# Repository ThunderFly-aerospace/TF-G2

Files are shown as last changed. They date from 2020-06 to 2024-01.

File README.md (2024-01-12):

# TF-G2 - Unmanned Autogyro Development Kit




Click on the following video to quickly get an overview: 
ThuderFly_TFG2_training_autogyro_prototype (http://www.youtube.com/watch?v=6PtS-MwnM_8)

[TF-G2](https://www.thunderfly.cz/tf-g2.html) autogyro is well-suited for training UAV operators and for gaining experience with autogyro mission planning. TF-G2 is limited to light payloads, but it shares all the specific properties of larger autogyros in our offering. It may find application in less demanding flight operations, however, its main purpose is to be a tool for low-cost application practice. The autogyro’s small size leads to easy transport, repairs, and maintenance.
To enhance the ease of learning autogyro technology, we made it possible to [simulate TF-G2 flight](https://github.com/ThunderFly-aerospace/PX4-FlightGear-Bridge) prior to the real flight training.

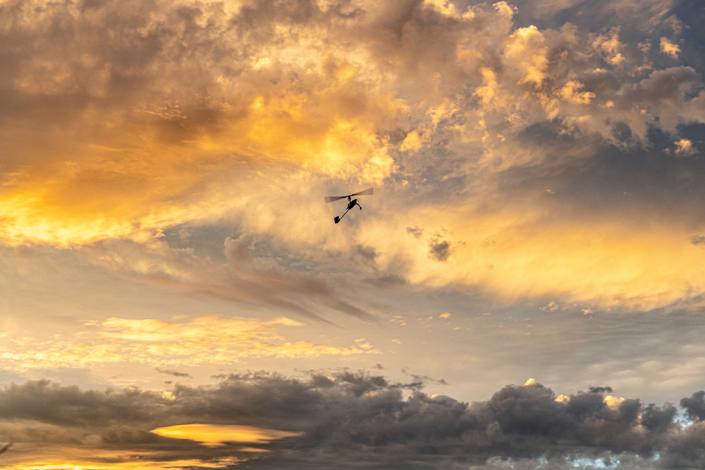
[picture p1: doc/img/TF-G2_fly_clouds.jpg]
TF-G2 during flight


## The main design highlights

  * Micro payload load capacity suitable for multiple types of [TF-ATMON atmospheric sensors](https://www.thunderfly.cz/tf-atmon.html)
  * Low audible noise
  * High maneuverability and agility
  * Extreme tolerance to rotor blade damage
  * Repairabile and low maintenance
  * Use of 3D printing flexibility
  * [Simulation model available](https://github.com/ThunderFly-aerospace/FlightGear-TF-G2)
  * [Car roof takeoff ready](https://github.com/ThunderFly-aerospace/TF-SIMPLEPLATFORM)

Based on that features the TF-G2 is perfectly suitable for [atmospheric measurement applications](https://www.thunderfly.cz/tf-atmon.html). That could be illustrated by the [successful integration of multiple sensor types](https://github.com/ThunderFly-aerospace/TFUNIPAYLOAD01). 

## Applications
Here are some examples of existing use cases for TF-G2 as a lightweight sensor carrier. These application-specific use cases extend the integrated sensing possibilities provided by existing autogyro avionics. The inherently existing onboard sensors in avionics are position, time, wind speed direction and velocity, and atmospheric pressure.

### Particulate matter sensing

Particulate matter sensing in the atmosphere is a scientific technique used to monitor and measure the concentration of small solid particles suspended in air, often termed as aerosols. These particles, typically categorized by their size - such as PM2.5 and PM10 - can originate from various sources including combustion processes, industrial emissions, vehicle exhausts, and natural phenomena like dust storms. Sensing and monitoring particulate matter is crucial for environmental health and public safety, as high levels can severely impact air quality, contributing to respiratory and cardiovascular diseases. Moreover, this data aids meteorological predictions and climate models, as particulates influence atmospheric visibility, and can affect the earth's radiation balance, hence playing a role in climate change. The TF-G2 autogyro could be equipped by [TFPM01](https://github.com/ThunderFly-aerospace/TFPM01) particulate matter sensor to measure the concentration of particulate matter in the specified air volume. 

Watch the video (https://www.youtube.com/watch?v=KUhktPDEi8I)

### Humidity and temperature sensing

Humidity and temperature sensing in [atmospheric vertical sounding](https://en.wikipedia.org/wiki/Atmospheric_sounding) involve the measurement of atmospheric moisture content and temperature at various altitudes. Instruments like the [TFHT01 sensor](https://github.com/ThunderFly-aerospace/TFHT01)  from ThunderFly are pivotal in collecting this data. These compact and lightweight sensors, designed specifically for UAV applications, can withstand varied atmospheric conditions and provide accurate, high-resolution measurements. Acquiring this data is essential for meteorological forecasts and climate studies, as the vertical distribution of temperature and humidity influences weather patterns, storm development, and overall climate dynamics. The [TFHT01](https://github.com/ThunderFly-aerospace/TFHT01) sensor, with its specialized design and precise data, has become an instrumental tool in advancing our understanding of these complex atmospheric processes.

TF-G2 atmospheric sounding experiment

An example of an atmospheric profiling experiment. The time difference between the reference and the experiment was around 6 hours. 

### Electric field monitoring

Electric field monitoring via TF-G2 UAV autogyro near thunderstorms entails the measurement of atmospheric electrical properties associated with storm activities. The charged particles present in thunderstorms create strong electric fields, which can be accurately detected and monitored by [THUNDERMILL01 sensor](https://github.com/UniversalScientificTechnologies/THUNDERMILL01). The TF-G2 autogyro, equipped with specialized sensors, can navigate challenging weather conditions and provide critical, real-time data on the strength and spatial distribution of the electric fields. Understanding these fields is crucial in predicting lightning activity, improving weather forecasts, and contributing to research on storm dynamics and atmospheric electricity. This UAV-autogyro technology offers a unique, mobile platform to safely investigate these intense electrical phenomena without putting human lives at risk.

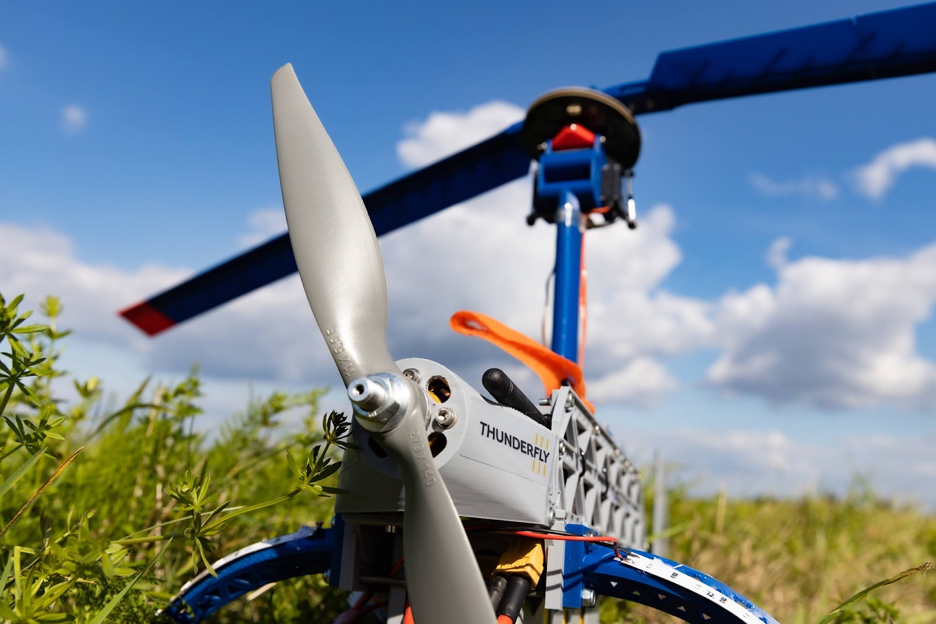
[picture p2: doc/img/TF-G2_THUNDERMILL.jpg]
TF-G2 with installed THUNDERMILL electric field sensor


### Ionising radiation monitoring

Ionizing radiation monitoring in the atmosphere involves detecting and quantifying radioactive particles using specialized devices like semiconductor-based ionizing radiation [AIRDOS03](https://www.ust.cz/UST-dosimeters/AIRDOS/#airdos03-uavdos) spectrometer and dosimeter. This instrument measures the intensity and spectral distribution of ionizing radiation, such as alpha, beta, gamma, and X-ray emissions that can originate from natural sources or human activities. The compact and precise nature of semiconductor-based devices allows for sensitive detection and accurate quantification of radiation levels. Monitoring atmospheric ionizing radiation is vital for assessing environmental radiation hazards, managing nuclear emergencies, and supporting research in fields such as meteorology, geology, and climate science. These advanced devices help ensure public safety and enhance our understanding of natural and anthropogenic radioactive processes in the atmosphere.

## Why autogyro? 

Autogyro

In contrast to the well-known [VTOL](https://en.wikipedia.org/wiki/VTOL) aircraft designs. The autogyro could be considered a short take-off and vertical landing aircraft ([STOVL](https://en.wikipedia.org/wiki/STOVL)). Therefore it is suitable for a wide range of different applications. The main advantages to other well-known airframes: 

* Ability to take off and land using only a very short runway (almost zero length).
* High resistance to weather conditions, especially gusts of wind or thermals.
* A unpowered rotor enabling it to operate in an autorotation mode (one of the helicopter’s emergency modes as well). Consequently, it does not need to actively change a flight mode in case of failure (it does not need a parachute or other actively working devices). Its flight is thus inherently stable and safe at all times.
* Autogyro has significantly reduced audible noise due to the slowly rotating rotor and propeller. 
* Absence of a downwash - during take-off or landing the creation of an unwanted swirling of dust is eliminated.
* Low lift-to-drag ratio that can be adjusted by construction parameters. This ability can be useful because an unmanned autogyro cannot fly very far in the case of controls failure (as is the case of a conventional airplane), the flight is still safe and the autogyro cannot fall (as is typical for multi-copters or wrongly piloted helicopters).

The autogyro has generally many construction variants. The one, which is in the scope of this repository has a fully tilted rotor. The main advantage of this construction feature is obtaining better controllability over its wide airspeed range. It can also be controlled down to zero forward airspeeds, compared to a classical rudder/elevator setup.

## Repository content

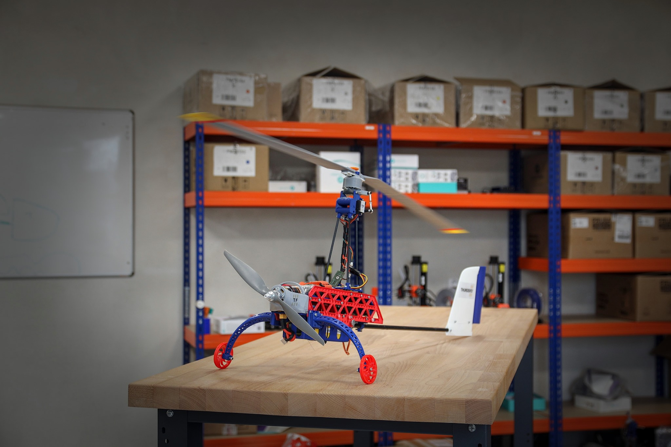
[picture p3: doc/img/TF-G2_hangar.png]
TF-G2 in hangar


This repository contains open-source design files of the autogyro construction. Most components are 3D-printed. However, the printable data (gcodes) are generated by our special software suite - processor3D. It is required that parts are sliced properly according to the material to make sure that resulted in 3D-printed parts could be used safely for the flight. **Therefore for safety reasons we do not recommend attempting to slice the parts yourself. It is better to contact us.**

The product, support, or accessories could be obtained from [ThunderFly s.r.o.](https://www.thunderfly.cz/), via an email to info@thunderfly.cz .

### Contribution

In case you want to contribute to the open-source project we have a [contribution guideline](https://github.com/ThunderFly-aerospace/TF-G2/blob/4s/CONTRIBUTING.md). Your contribution is very welcome! For a contribution, you can get access to the optimized and safe printable files (gcodes).

## References 

* [TF-G2: PX4 powered autogyro](https://static.sched.com/hosted_files/px4summit2021/ca/TF-G2%20PX4%20powered%20autogyro.pdf)
* ["Flight control system for a small autogyro" bachelor thesis](https://dspace.cvut.cz/handle/10467/101004)

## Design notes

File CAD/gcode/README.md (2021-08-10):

# TF-G2 autogyro printable gcodes

The printable data (gcodes) are generated automatically by our special software suite. It is required to ensure safety of printed parts. **Therefore for safety reasons we do not recommend to attempt to slice the parts yourself.**

The support for the product could be obtained from [ThunderFly s.r.o.](https://www.thunderfly.cz/), via an email to info@thunderfly.cz .

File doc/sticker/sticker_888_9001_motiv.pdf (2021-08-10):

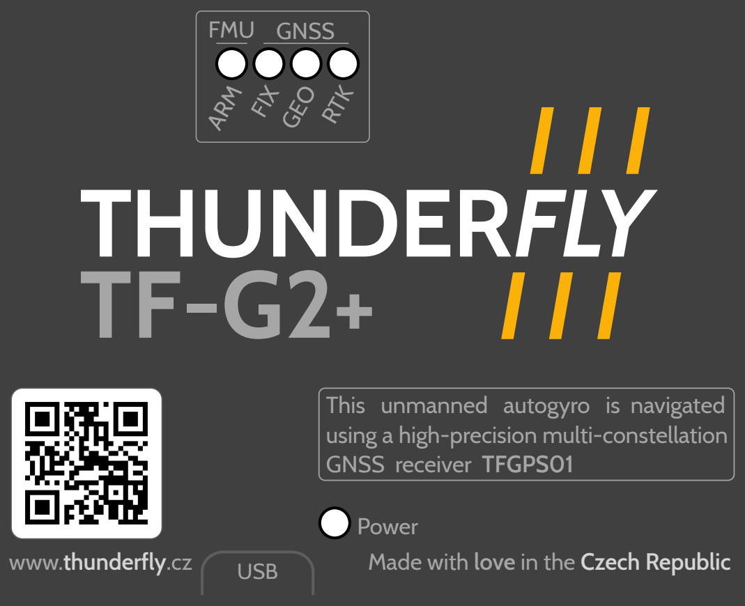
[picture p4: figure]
USB; Power; This unmanned autogyro is navigated using a high-precision multi-constellation GNSS receiver TFGPS01; ARM FIX; GEO RTK; FMU GNSS

www.thunderfly.cz | Made with love in the Czech Republic

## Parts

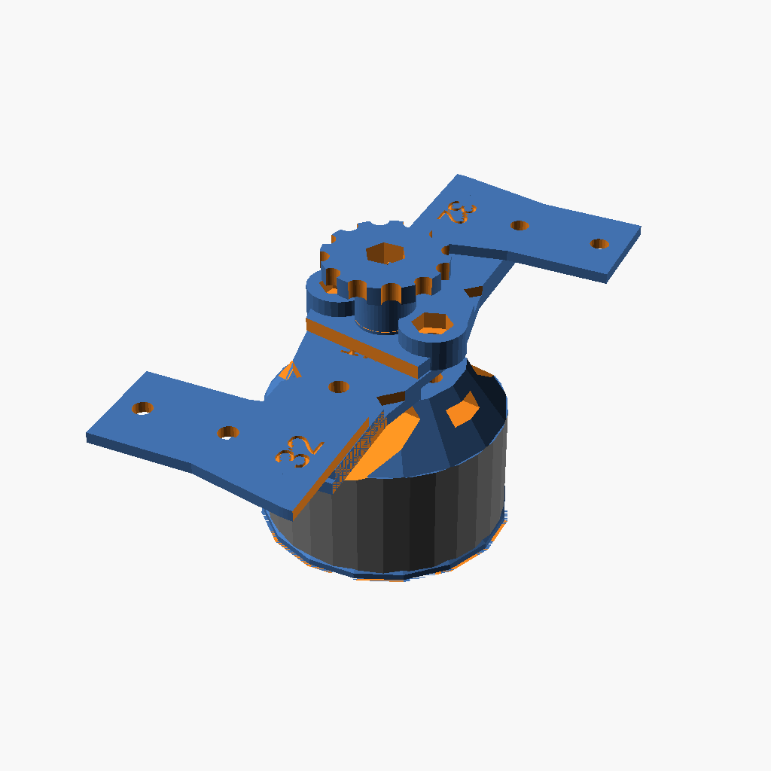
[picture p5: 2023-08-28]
CAD/png/position_rotor_parts.png

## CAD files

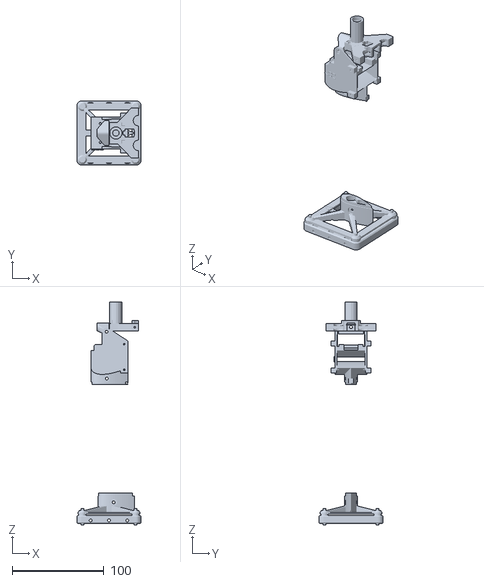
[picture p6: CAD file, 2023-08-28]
CAD/stl/assembly_pylon.stl
70.0 x 70.0 x 243.1

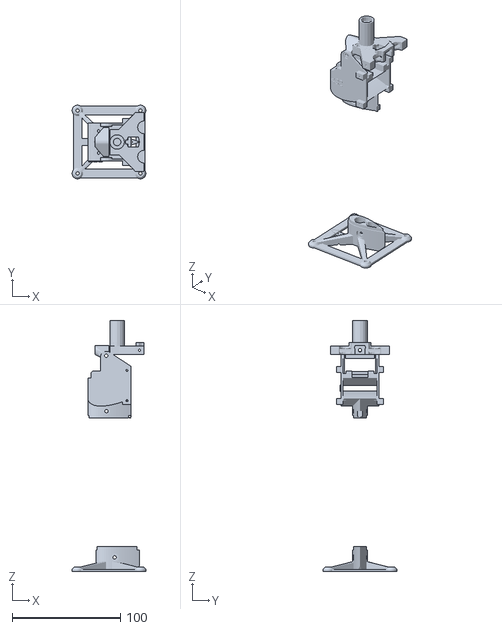
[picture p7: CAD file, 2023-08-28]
CAD/stl/assembly_rotor_head.stl
68.0 x 67.9 x 231.4

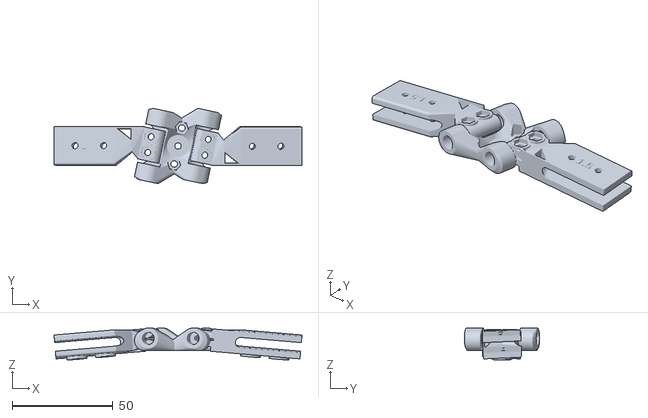
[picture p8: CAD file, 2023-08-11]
CAD/stl/assembly_freeflap.stl
122.8 x 37.3 x 15.8

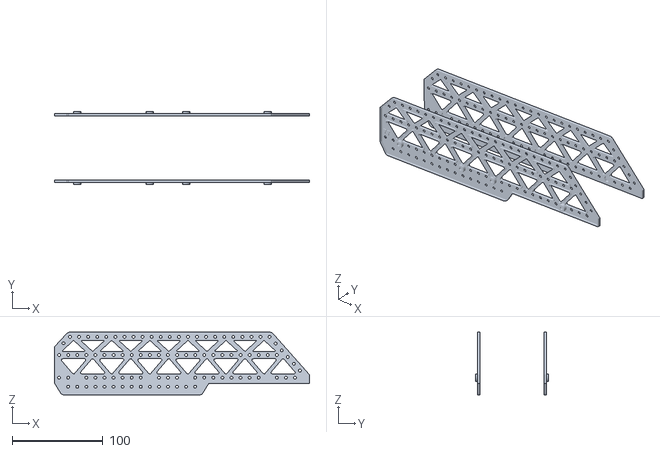
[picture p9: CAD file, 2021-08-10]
CAD/src/build_manual/stl/buildmanual_0001_c.stl
281.1 x 80.0 x 69.2

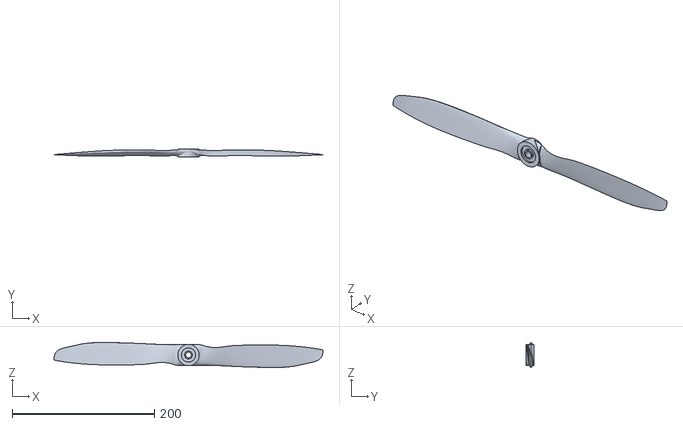
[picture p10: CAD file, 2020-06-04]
CAD/src/external_parts/APC_15x4C.stl
378.9 x 11.0 x 35.3

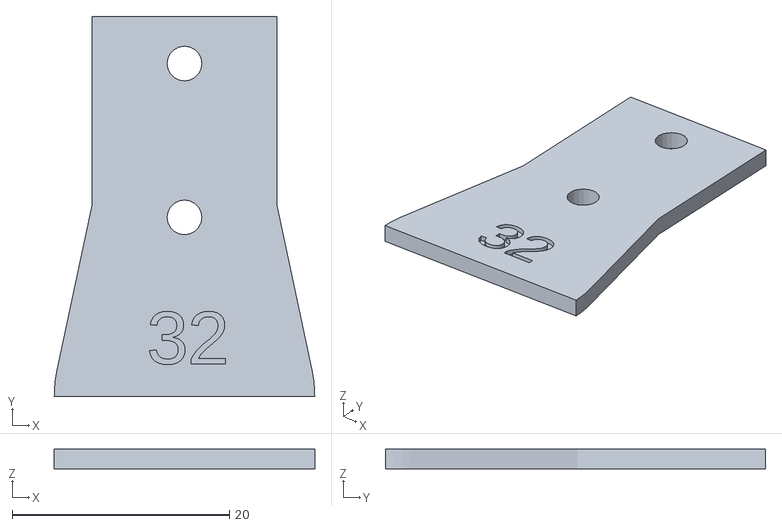
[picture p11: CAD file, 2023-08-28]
CAD/stl/888_4006.stl
24.0 x 35.0 x 1.80

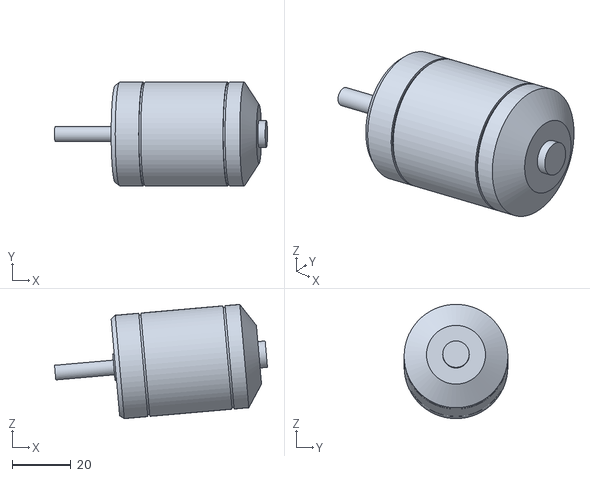
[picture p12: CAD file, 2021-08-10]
CAD/src/build_manual/stl/buildmanual_motor.stl
72.2 x 35.2 x 38.8

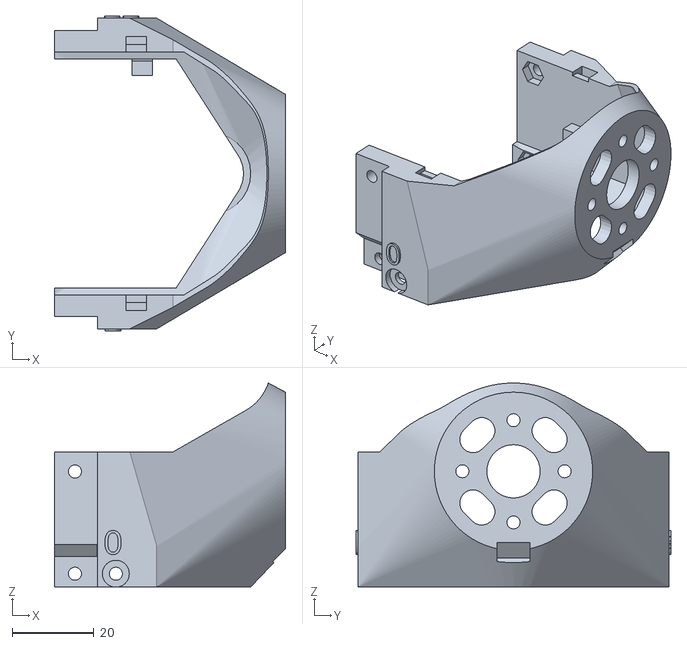
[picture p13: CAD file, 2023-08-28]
CAD/stl/888_1002.stl
56.5 x 77.0 x 49.9

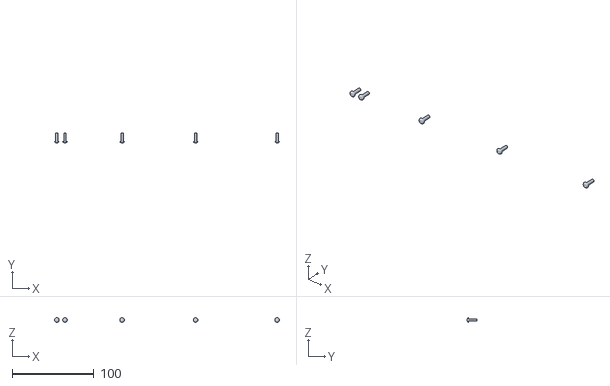
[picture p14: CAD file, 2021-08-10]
CAD/src/build_manual/stl/buildmanual_0001_d.stl
275.7 x 11.7 x 5.70

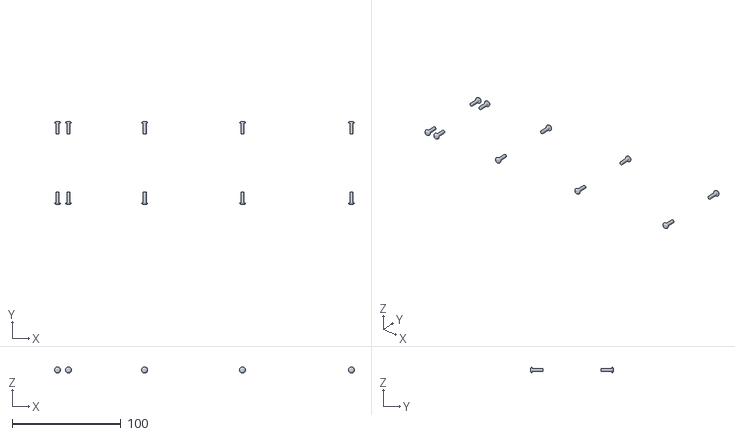
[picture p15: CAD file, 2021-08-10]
CAD/src/build_manual/stl/buildmanual_srouby_bocnice.stl
275.7 x 76.5 x 5.70

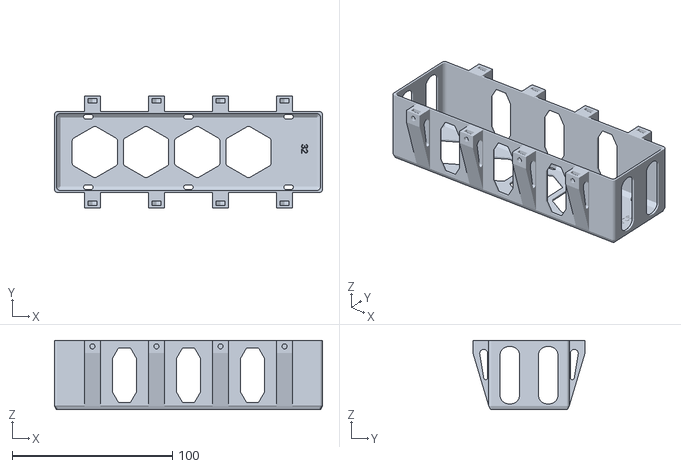
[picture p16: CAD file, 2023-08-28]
CAD/stl/position_888_1018.stl
167.4 x 70.0 x 43.2

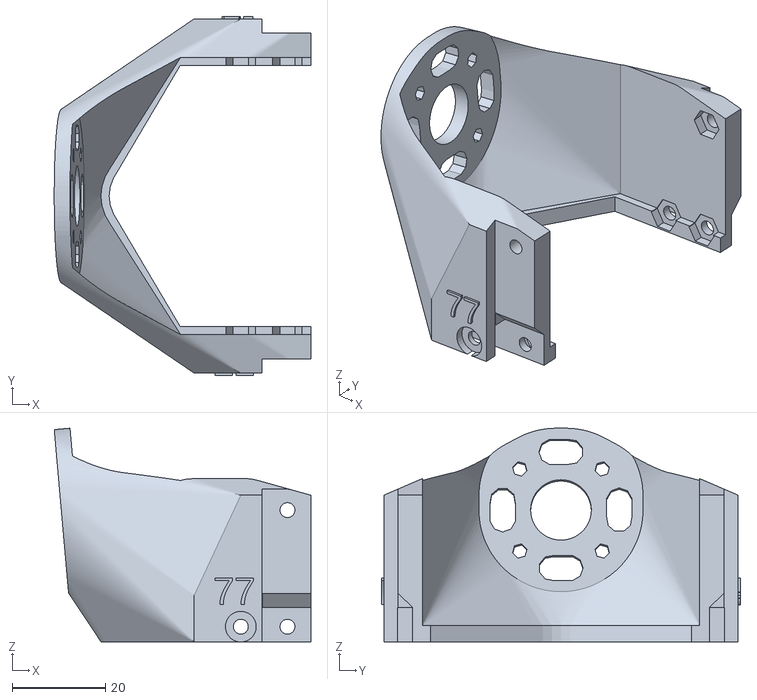
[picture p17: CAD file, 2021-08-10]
CAD/src/build_manual/stl/buildmanual_0001_b.stl
55.0 x 77.0 x 45.8

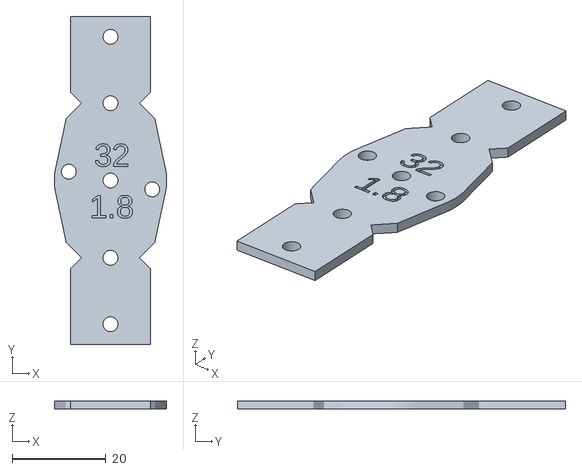
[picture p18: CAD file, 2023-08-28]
CAD/stl/888_4002.stl
24.0 x 70.0 x 1.80

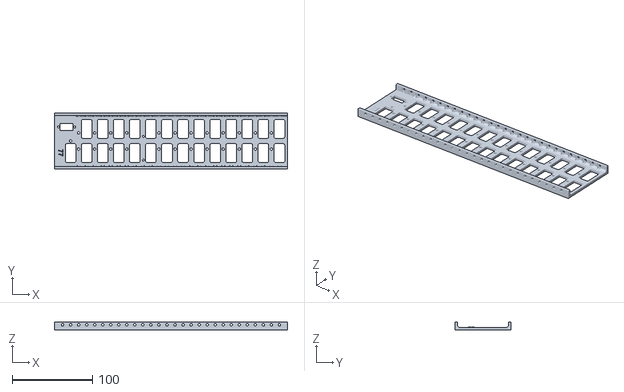
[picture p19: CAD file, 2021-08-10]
CAD/src/build_manual/stl/buildmanual_0001_a.stl
290.0 x 70.0 x 9.50

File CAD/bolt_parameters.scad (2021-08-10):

/// deprecated parameters - should be removed after code upgrade to latest libraries
///

// screw length step - minimum difference in length between two types of screws
basic_screw_length = 5;

//Screw diameter and nut for M6 [mm]
M6_screw_diameter=6.5;
M6_head_diameter = 10+0.5;
M6_head_height = 6;
M6_nut_height = 4.9;
M6_nut_diameter = 11.8;
M6_nut_pocket = 10.4;

//Screw diameter and nut for M5 [mm]
M5_screw_diameter=5.5;
M5_head_height = 5;
M5_head_diameter = 13+0.5;
M5_nut_height = 4.5;
M5_nut_diameter = 9.4;
M5_nut_pocket = 8.4;

//Screw diameter and nut for M4 [mm]
M4_screw_diameter=4.5;
M4_screw_head_height = 4;
M4_nut_height = 3.2;
M4_nut_diameter = 8.4;
M4_nut_pocket = 7.5;

//Screw diameter and nut for M3 [mm]
M3_screw_diameter = 3.2;
M3_nut_height = 2.7;
M3_nut_diameter = 6.6;
M3_screw_head_height = 3;
M3_nut_pocket = 5.6;
M3_head_diameter = 6.6;
M3_head_diameter_ISO7380 = 7.6; //https://eshop.killich.cz/signys_data/eobchod/navody/katalog/strany/iso7380a.pdf
M3_head_height = 3.0;


//Screw diameter and nut for M2,5 [mm]
M2_5_screw_diameter = 2.7;
M2_5_nut_height = 2.3;
M2_5_nut_diameter = 6;
M2_5_nut_pocket = 5.1;

//Screw diameter and nut for M2 [mm]
M2_screw_diameter = 2.0;
M2_nut_height = 1.8;
M2_nut_diameter = 4.8;
M2_nut_pocket = 3.95;
M2_head_diameter = 4.5;
M2_head_height = 2.0;

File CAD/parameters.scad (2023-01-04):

include <bolt_parameters.scad>
use <./src/lib/stdlib/naca4.scad>

week = "77";  // dummy value for visual rendering not used for printing.

global_clearance = 0.2;
clearance = global_clearance;

layer_thickness = 0.2;
base_patern = 10;

gliding_angle = 14;         // tenhle úhel by se zřejmě v budoucnu měl počítat z požadované klouzavosti.



////Simoniny parametry pro nosník rotoru
base_length = 290; //delka podlozky
base_split_position = [0, 149, base_length];
base_width = 70; //sirka podlozky - vnější šířka nosníku
base_thickness = 3; //vyska podlozky
autopilot_base_thickness = 4; // vyska podlozky vysuzujici prostor pod autopilotem
rantl_thickness = 3; //sirka steny podlozky
rantl_height = 6.5;
niy=4; //pocet der podelne

side_base_thickness = 0.2*6; // minimalni tlouska  u bocnic napr. sten



// Rotor parameters

rotor_blade_AOA = 1.5;      // nastavení úhlu náběhu rotorového listu
rotor_blade_rod = true;  // generovat diru pro uhlikove tycky
rotor_blade_length = 500;   // délka rotorového listu
// rotor_blade_length = 450 - 15;   // délka rotorového listu -- nastaveni prvniho vytisku
//rotor_blade_length = 460;   // délka rotorového listu
rotor_blade_depth = 45.5+2;     // hloubka rotorového listu
rotor_balde_tip_cutoff = 15.5;

blade_mount_length = 30;

blade_mount_width = 17;
blade_mount_thickness = 4.6;
blade_mount_screw_offset = 5; // distance of first screw from rotor end

// Testovaci maly rotor
    /*
    rotor_blade_rod = false;
    rotor_blade_length = 145;   // délka rotorového listu
    rotor_blade_depth = 45.5 * (145/385);     // hloubka rotorového listu
    blade_mount_length = 20;
    blade_mount_width = 10;
    blade_mount_thickness = 4;
    */
// konec parametru pro testovaci maly rotor

rotor_height = 180;         // výška otočného kloubu rotoru nad hlavní trubkou vírníku (odhad)
rotor_blades_count = 2;
rotor_delta_angle = 12;
rotor_blade_thickness = 5.1;
//rotor_balde_tip_cutoff = 10;

rotor_blade_naca = 2412;
rotor_blade_parts_count = 4;
//rotor_blade_parts_count = 3;

blade_transition_length = 10; // length of blade transition

blade_mount_screw_distance = (16.47+11.86)/2;

rod_from_end = 10;

/* blade_shell_thickness = 0.4;
blade_shell_thickness_inner = 0.4;
blade_shell_thickness_wire = 0.4;
blade_infill_distance = 25;
blade_infill_overlap = 0; */

/// Nastaveni pro Slic3r
blade_shell_thickness = 0.5;
blade_shell_thickness_inner = 0.08;
blade_shell_thickness_wire = 0.5;
blade_infill_distance = 23;
blade_infill_overlap = 0;

//blade_rod_position = [rotor_blade_depth/4 + 5, 0, 0];
//blade_rod_position2 = [rotor_blade_depth/4 - 5, 0, 0];

//blade_rod_position = [15, 0, 0];
//blade_rod_position2 = [4, 0.3, 0];

//blade_rod1_diameter = 2.58;
//blade_rod2_diameter = 2.58;
//blade_rod3_diameter = 2.13;
blade_rod1_diameter = 2.45;
blade_rod2_diameter = 2.45;
blade_rod3_diameter = 2.45;


// blade_rod1_position = [3.4, 0.3, 0];

blade_rod1_xposition = rotor_blade_depth/4 - 8.9;
blade_rod1_yposition = rotor_blade_depth * camberY(naca = rotor_blade_naca, x = blade_rod1_xposition / rotor_blade_depth); // calculate airfoil chamber line y position

blade_rod1_position = [blade_rod1_xposition, blade_rod1_yposition, 0];  // shift rod1 to chamber line location
blade_rod2_position = [rotor_blade_depth/4 - 5.8, 0.5, 0];
blade_rod3_position = [rotor_blade_depth/4 + 3.5, 0.5, 0];

blade_glue_holes = 0;

blade_mount_screw = M3_screw_diameter;
blade_mount_nut = M3_nut_diameter;

rotor_blade_endtip_diameter = 20;

rotor_blade_part_list = [0, 50, 200, 350, 500];


// vzdalenosti der pro kryty
//platform_mount_points = [base_patern*5, base_patern*13, base_patern*17, base_patern*26];
// Otvory pro pripevneni na platformu
platform_mount_points = [base_patern*8, base_patern*26];

cover_rantl_thickness = 0.8; // tloustka rantlu, ktery ma mit ramecek pro pripevneni a zpevneni oblecku.. 

leg_screw_dy = 20; // Vzdalenost sroubu, na ktery se upevnuji podvozkove nohy

/////
// Parametry rotorové hlavy
/////


// Parametry pro loziska rotoru

bearing_outer_diameter = 10.2;
bearing_thickness = 4;
bearing_shaft_length = 20.6;


////
//
//	Navrh geometrie rotorove hlavy vychazi z nakresu od Dobiase
//
////

rotor_head_plate_thickness = 5;
rotor_ball_joint_neck = 3; // vyska krcku tahla od stredu koule.


// parametry pro dil, co se naklapi v roll a pitch, obsahuje tfprobe

// delka dilu v podelne ose virniku - od osy pitch
rotor_head_rod_x = 35;
// sirka dilu na stredy tahel
rotor_head_rod_y = rotor_head_rod_x*2 - rotor_ball_joint_neck*2;
// vyska dilu az po rovinu rotoru
rotor_head_rod_z = 0;

rotor_head_shaft_angle = 10;



rotor_head_pitch = 0;
rotor_head_roll = 0;



// Engine and engine holder parameters

motor_holder_height = base_patern * 5;
motor_holder_thickness = 3.5;
motor_holder_motor_height = 25;
motor_holder_side_mount_height = base_patern*2.5;
pylon_holder_side_mount_height = base_patern*4.5;

engine_angle = 0; // ongle of engine axis relative to fuselage main axis
engine_diameter = 55;
engine_offset = 53;			// Posun motoru v ose X (dopredu)




// Parametry pro hacek na kabely od motoru
	motor_wire_holder_width = 5;
	motor_wire_holder_height = 10;
	motor_wire_holder_space = 3;
	motor_wire_holder_thickness = 2.5;
	motor_wire_holder_z_shift = 10;
	motor_wire_holder_x_shift = 19;

// Parametry pro ochranny ram nad motorem
	motor_protective_frame_x_shift = 20;
	motor_protective_frame_z_base = 32;
	motor_protective_frame_beam_width = 5;
	motor_protective_frame_beam_thickness = 3;
	motor_protective_frame_width = base_width-3;
	motor_protective_frame_plug_thickness = 2;
	motor_protective_frame_plug_length = 4;
	motor_protective_frame_thickness = 5;
	motor_protective_frame_z_scale = 0.75;


//sroub servo
Servo_screw = 1.5;
Servo_nut_height = 1;
Servo_nut_diameter = 2.7;

tail_pipe_d = 13.04;

// elevator parameters

elevator_pitch = 2; // elevator pitch relative to main fuselage axis

/// rudder parameters

rudder_height = 150;
height_bottom_part = 130;
rudder_depth_max = 200;
rudder_inclination = 25;

below_rudder_height = 30;
rudder_depth = 60;

tail_airfoil_n = 80;

//center_of_gravity_position = [main_pylon_position - tan(gliding_aggle)*rotor_height, 0, 0];


////landing gear

radius_undercarriage = 25;
vzdalenost_x = tan(20) * 131;
vzdalenost_y = (131 - radius_undercarriage)/tan(79);
uhel_y = 90 - 20;
uhel_x = 90 - 79;

maximum_printable_size = 150;

// FIXME: Jak zapnout figerglass z procesoru3d ?
// fiberglass_gear = false;


// Rotor pylon parameters


// pylon_height = 250 - pylon_holder_side_mount_height;

pylon_pipe_counterbore = 24;  // delka zapusteni pylonove tyce do dilu nahore
pylon_pipe_counterbore_bottom = 20;  // delka zapusteni pylonove tyce do dilu dole
pylon_pipe_screw_distance_from_top_end =  17;
pylon_pipe_screw_distance_from_bottom_end =  10;


pylon_pipe_top_offset = 6; // Jak hluboko do TFSLOTU lze tycku pylonu zapustit..
pylon_airfoil_shell_overlap = 3;  // presah profilu (krytu) pylonu a montaznich casti (spodnyi a horni objimka)

pylon_pipe_d = 10.3;
pylon_suspension_height = 150;
pylon_pipe_top_dist = 0;
pylon_thickness = 0; // Netusim, co to je

pylon_bottom_wall = 5;

pylon_silentblocks_base_distance = 58;    // vzdalenost silentblocku pylonu od sebe
pylon_pipe_top_y_dist = 25;
pylon_pipe_top_x_dist = 30;
pylon_screw_top_y_dist = 25;
pylon_screw_top_x_dist = 15;

pylon_height = 180 + 50 - pylon_holder_side_mount_height;

airspeed_width = 35;
airspeed_naca = 0004;
airspeed_dist = 20;


// Parametry k akumulatoru

//battery_type = "Zippy_4S_3700";
//  GensACE 3300 mAh

//free-flap-head
free_flap_ax_length=36;
free_flap_ax_diameter=3;

free_flap_bearings_length=9.8;
free_flap_bearings_outer_diameter=6.2;
free_flap_bearings_ring_diameter=9;
free_flap_bearings_ring_h=1.5;
//free_flap_bearings_outer_diameter=3;
free_flap_negativ_flap_limit=5;
free_flap_bearing_add=4;
free_flap_desk_add=1;
free_flap_desk_h=2.5;

free_flap_delta_angle=-rotor_delta_angle;
free_flap_blade_screw_distance=blade_mount_screw_distance;
free_flap_central_part_screw=3;
free_flap_central_part_screw_distance=3 + 4.5 + blade_mount_screw/2;

free_flap_circle_fn=40;

free_flap_ax_offset=6+free_flap_bearing_add/2+free_flap_bearings_outer_diameter/2;

free_flap_shaft_l=free_flap_ax_length-2*free_flap_bearings_length;
free_flap_shaft_h=free_flap_ax_diameter+free_flap_bearing_add;
free_flap_shaft_neck_l=7;

free_flap_cut_d=12;
free_flap_cut_h=10;
free_flap_cut_w=5;

free_flap_blade_d=20;
free_flap_blade_holder_h=3;

free_flap_blade_holder_l=blade_mount_length;
free_flap_blade_h=blade_mount_thickness+0.5;
free_flap_blade_w=19;
free_flap_blade_first_screw=blade_mount_screw_offset+0.5;

free_flap_blade_holder_radius=0.7*free_flap_blade_holder_h;


//if(battery_type == "GensACE_3S_3300"){
	// battery_case_height = 25;
	// battery_case_start_x = 25;
	// battery_case_wall = 1;

	// battery_width = 50;
	// battery_height = 20;
	// battery_length = 150;

	// battery_capacity = 3300;
	// battery_cells = 3;
//}
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

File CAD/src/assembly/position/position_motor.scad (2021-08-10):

include <../../../parameters.scad>
use<../../lib/stdlib/motors.scad>

translate([base_patern*3, 0, motor_holder_side_mount_height])
translate([0, 0, 4])
rotate([0, -90-5, 0]) motor_c3548_900();

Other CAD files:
CAD/amf/printplate_888_1016_front.amf
CAD/stl/888_4008.stl
CAD/stl/888_1010.stl
CAD/stl/position_rotorhead.stl
CAD/src/build_manual/src/buildmanual_motor.scad
CAD/blender/TF-G2_flow.blend
CAD/blender/colours.blend
CAD/blender/title.blend
CAD/src/888_1001.scad
CAD/src/888_1002.scad
CAD/src/888_1003.scad
CAD/src/888_1004.scad
CAD/src/888_1006.scad
CAD/src/888_1007.scad
CAD/src/888_1008.scad
CAD/src/888_1009.scad
CAD/src/888_1010.scad
CAD/src/888_1011.scad
CAD/src/888_1012.scad
CAD/src/888_1013.scad
CAD/src/888_1018.scad
CAD/src/888_1019.scad
CAD/src/888_1020.scad
CAD/src/888_1021.scad
CAD/src/888_2002.scad
CAD/src/888_2003.scad
CAD/src/888_2004.scad
CAD/src/888_2005.scad
CAD/src/888_2006.scad
CAD/src/888_2007.scad
CAD/src/888_3001.scad
CAD/src/888_3002.scad
CAD/src/888_3004.scad
CAD/src/888_3006.scad
CAD/src/888_4001.scad
CAD/src/888_4002.scad
CAD/src/888_4003.scad
CAD/src/888_4004.scad
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

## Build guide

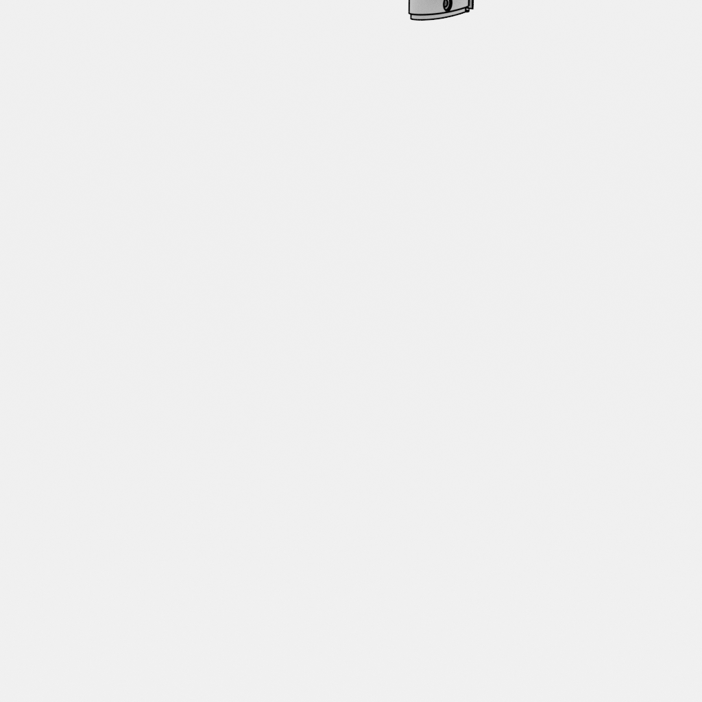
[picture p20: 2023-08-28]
doc/assembly_guide/img/TF-G2_assembly_rotorhead_complete.png

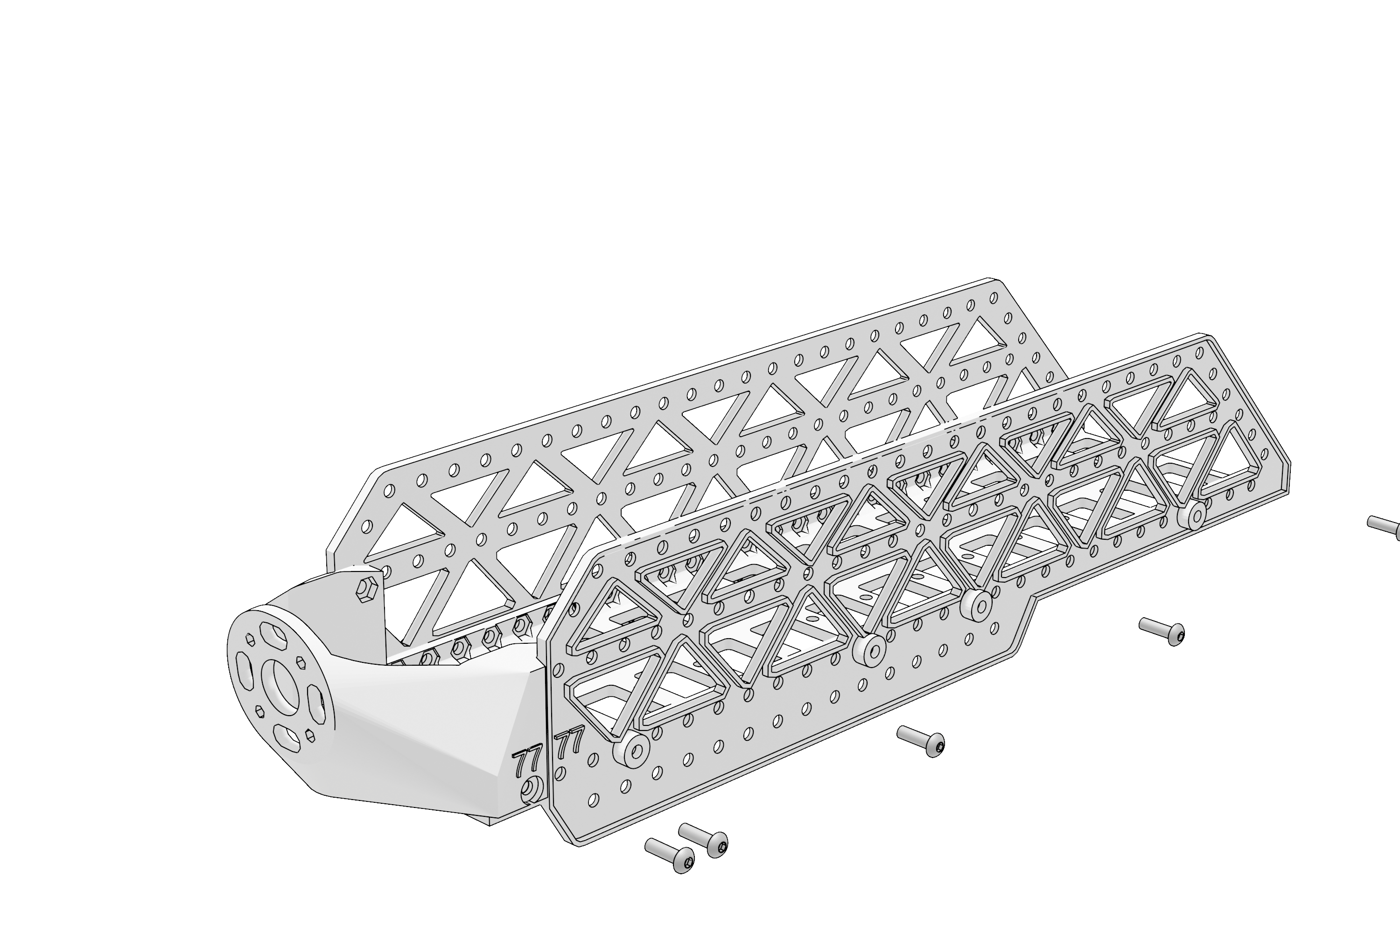
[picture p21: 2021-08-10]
doc/assembly_guide/src/buildmanual_0001.png

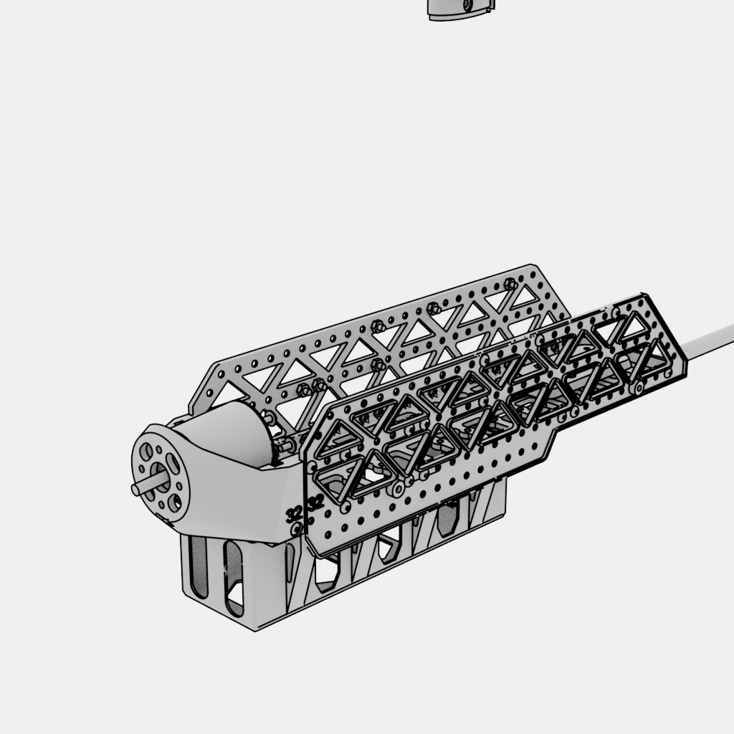
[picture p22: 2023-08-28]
doc/assembly_guide/img/TF-G2_assembly_chassi.png

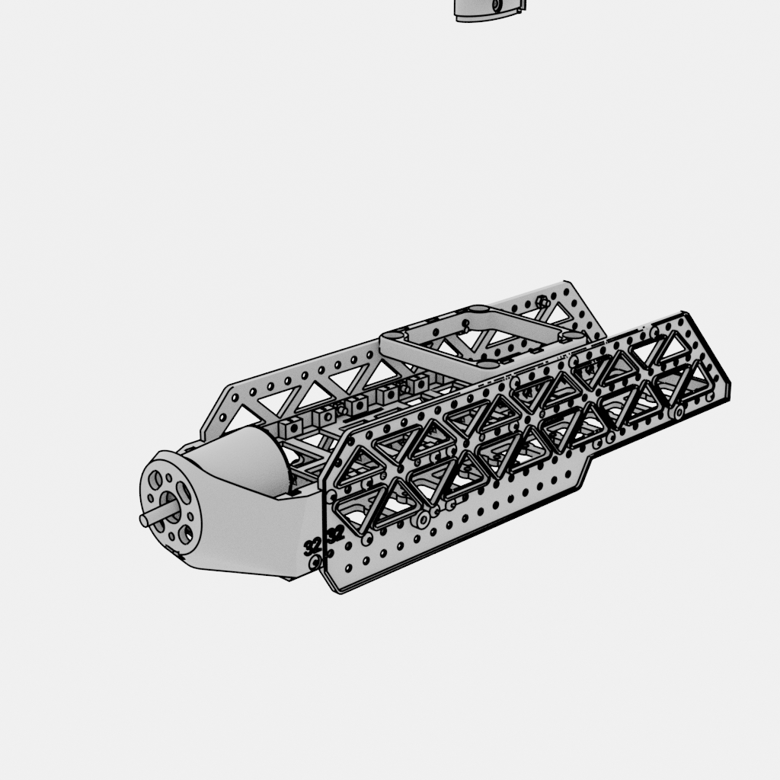
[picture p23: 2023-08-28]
doc/assembly_guide/img/TF-G2_assembly.png

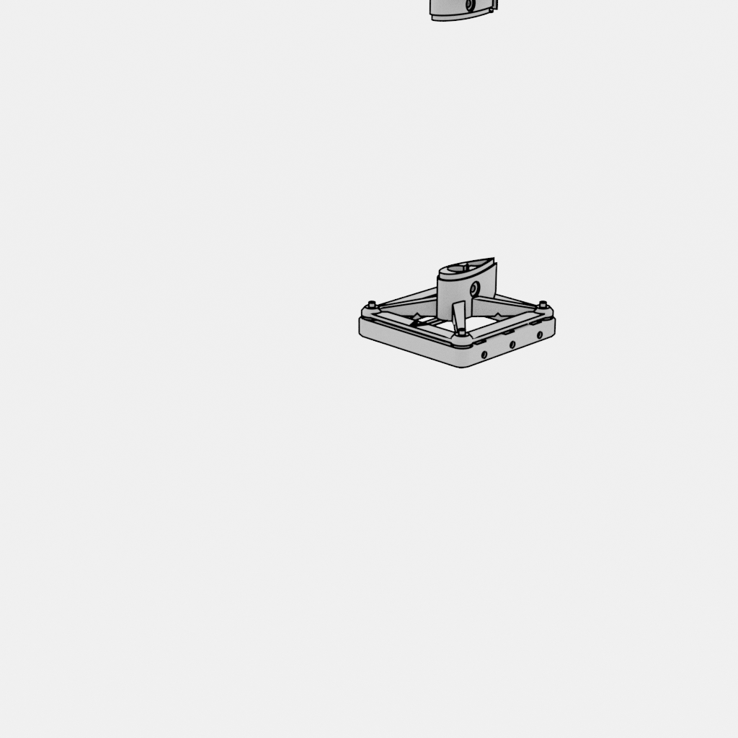
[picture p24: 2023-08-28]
doc/assembly_guide/img/TF-G2_assembly_pylon.png

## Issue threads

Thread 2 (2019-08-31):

Nosná podložka

roman-dvorak, 2019-08-31:
K dovyřešení:
- [ ] Vyřešit způsob připevnění předního podvozku.
---
 - [X] Základní návrh (done by @zelenac)
 - [X] Úprava rozměrů a prvotní vytvoření odlehčovacích otvrů (done by @roman-dvorak)
 - [x] Optimalizace hmotnosti: Chytřejší otvory pro odlehčení
 - [x] Místo na připevnění podvozku
 - [x] Zapuštění matek v postranním rantlu.
 - [X] Rozšířit podložku o 10 mm (celková šířka 70 mm), @roman-dvorak
 - [x] Chybí díra pro přišroubování držáku motoru do podložky.
---

Nosná podložka malého vírníku se bude skládat ze dvou identických částí.

Budou to 2 destičky, které se následně vzájemně sešroubují ~pomocí nějaké vytištěné spojky~.
Destička bude mít podélně vyšší límec, který bude mít dva úkoly. Zpevnění celé konstrukce. Vytvoření míst pro připevnění bočních stěn.

~Podložka bude 55 mm široká a dlouhá 2x140 mm~ (staré údaje). Tato délka byla zvolena z technologických důvodů - maximální tiskový rozměr.

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

Příčný řez dílem
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

Ve spodní části budou díry na šrouby na připevnění dalšího příslušenství. Budou zarovnané do nějaké určité mříže. Předpokládám nějakých 4-5 řad. Budou to díly na M3 šrouby.

Všechny rozměry musí být udělány pomocí proměnných parametricky.

roman-dvorak, 2020-04-02:
Nosná podložka je aktuálně ve stavu, že obsahuje boční lem s řadou děr pro připevnění bočnic. Podložka bude dělena na 2 časti. Na obrázku to je naznačeno. Bočnice budou na 3 časti a je potřeba zajistit, aby předěl částí nevycházel na stejné místo.

Od původního modelu došlo k odlehčení vytvořením vetších otvorů ve dnu modelu. Tyto otvory bude potřeba upravit v návaznosti na připevnění podvozku. Může pak být provedeno další odlehčení. Nebo ztečení či chytřejší vyztužení.

Na začátek první zprávy jsem vypsat věci k úpravě.

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

roman-dvorak, 2020-04-25:
Do podložky přidány šestihrany na zapuštění matky, upraveno odlehčení a otvory pro připevňení ocasu a předního podvozku.

kaklik, 2020-05-18:
Ten způsob připevnění předního podvozku na dva šrouby je podle mě vyhovující.

Closed 2020-05-25.

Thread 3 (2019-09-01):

Díl pro připevnění tažného motoru

roman-dvorak, 2019-09-01:
- [X] Úvodní návrh
 - [X] Změna připevňení k bočnicím
 - [x] Zvětšení otvoru pro středovou osu na d=10mm
 - [x] Odstranění zubu (nevhodný pro tisk)
---
Druhý díl musí zapadnout do dílu #2 a bude přišroubován zespodu pomocí M3 šroubů. Bude to taková jednoduchá placka s výřezem na boční lem na #2.

Vnější rozměr musí být stejný jako rozměr podložky. Výška bude cca 7 cm.

Pro připevnění k základní podložce #2 budou v dílu z vnitřní strany kapsy na matky - jak vypadá kapsa je popsáno na konci.

Uprostřed placky bude otvor pro připevnění motoru. To bude realizované pomocí trojice děr uspořádaných do rovnostranného trojúhelníku. Poloměr kružnice opsané (skrze středy) bude cca 1.5 cm. Bude ještě upřesněno. Výšku motoru by mělo být možné nastavovat pomocí parametru.

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

Kapsa na matku je drážka (obdélníková díra) ukončená šestihranem v díře pro šroub. Matka se do ni zastrčí a následně se šroub může skrze díru přítáhnout.

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

roman-dvorak, 2020-04-02:
Oproti původnímu návrhu byl díl značně zmodifikován. Princip zůstává stejný.

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

Potřebné úpravy jsou zvetšení středové díry a upravení kulatého tvaru nahoře tak, aby se tam nevytvářel zub způsobený uchem pro připevňení.

Closed 2020-04-25.

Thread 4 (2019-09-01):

Boční stěny

roman-dvorak, 2019-09-01:
- [X] Základní návrh
 - [X] Ovory pro odlehčení (hardcodované)
 - [x] Odstranit starou řadu otvorů pro připevnění držáku motoru
 - [x] zparametrizovat a optimalizovat odlehčovací otvory
---
Boční stěny budou přišroubovány k límci dílu #2 a #3. Díl bude potřeba rozdělit na 3 části, čímž se zároveň zajistí, že spoj nebude vycházet na stejné místo jako bude spojen spodní díl #2.

Boční stěny by měly vypadat nějak cca takto:
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

Budou obsahovat řadu děr pro sešroubování s podložkou. Boční stěna může mírně přesahovat pod podložku #2.

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

Celková výška stěny by měla být okolo cca 8-9 cm. Délka cca 33 cm. Tloušťka stěny může být cca 3 mm. Pokud to bude málo, tak je následně možné nahoře domodelovat nějaké rozpěrky, které se tam buď přišroubují nebo zalepí.

Stěna by na sobě mohla mít také síť děr pro přišroubování nějakého příslušenství. Nemusí být tak hustá jako v podložce.

roman-dvorak, 2020-04-02:
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

Otvory pro odlehčení jsou dosti hardkodované. To by bylo vhodné trochu zparametrizovat. Dále v přední časti jsou 2 řady otvorů pro připevnění. To je důsledek kompatibility starší (už vytištěné verze držáku motoru) a nového umístění otvoru. Staré umístění děr je možné smazat.

Closed 2020-04-25.

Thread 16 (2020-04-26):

Doplnění airspeed senzoru

kaklik, 2020-04-26:
* [x] vytvořit víčko airspeed senzoru držící PCB TFASPDIMU
* [x] Upravit stávající řešení pro nový snímač [TFASPDIMU02](https://github.com/ThunderFly-aerospace/TFASPDIMU02)
* [x] Vyřešit umístění TFRPM viz issue: #76 (PCB z horní strany tak, aby byla snadno vidět LED)
* [x] Možná prodloužit TFSLOT trubici

Na vírník je potřeba přidat [airspeed senzor](https://github.com/ThunderFly-aerospace/TFAIRSPD01).

Uchycen by měl být na horní části pylonu pod rotorovou hlavou. viz issue: https://github.com/ThunderFly-aerospace/TF-G2/issues/7

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

@roman-dvorak  Navrhuje celý snímač namontovat místo středního dílu na fotografii výše.  Snímač by tak byl modifikovaný pouze pro tuto konstrukci.
Současný díl na fotografii jen vymezuje vzdálenost mezi bočnicemi pylonu. Druhý účel je, že určuje úhel těch bočních dílů a zajišťuje aby jeho vnitřní strany byly rovnoběžné.  Díl obsahující snímač by všechny tyto funkce mohl kombinovat.

roman-dvorak, 2020-04-26:
Úplně původně zamýšlené místo bylo pod tím středním rámečkem, kde jsou již připravené montážní otvory. Ale ten je dost nízko (původně měl být umístěný výš). Tak je možné ho nějak připevnit až přimo pod rotor. Do toho horního rámečku.

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

kaklik, 2020-06-05:
Myslím že mě napadlo jak zjednodušit úpravu z issue https://github.com/ThunderFly-aerospace/TFASPD01/issues/1
Tak aby snimač bylo možné umístit úplně nejblíže rotorové hlavě. Venturiho snímač by tak nově byl takováto krabička:

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

Zaoblené profily jsou ve skutečnosti nějaké NACA profily a jsou symetrické dva proti sobě.  Předpokládám, že by se celá tahle hranatá věc tiskla najednou, takže to může být i nějaká přepážka sloužící k vyztužení.
Je myslím zatím i jedno, jestli bude orientována horizontálně, nebo vertikálně.
Plošný spoj se snímači by se opět přimáčkl do kanálků z vnější strany a držel by tam tím že se celý snímač k něčemu přišroubuje.

kaklik, 2020-06-18:
@ChroustJan  navrhuje přes PCB s elektronikou udělat zasouvací víčko. Výhoda by byla, že se pak celý snímač dá vyndat jako samostatný celek a nehrozí že někde na louce vypadnou těsnění, nebo PCB.

kaklik, 2020-09-30:
@roman-dvorak  udělal první prototyp venturiho poličky. Zatím je poměrně masivní.

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

Chyby, které při návrhu vznikly jsou způsobeny nedokonalým převzetím konstrukce z anemometru.

- [ ] Plošný spoj se neopírá o přívodní konektor, ale je výše. Díky čemuž jej nelze dobře upevnit vůči vyústění trubiček
- [ ] Vyústění trubiček neobsahuje zúžení, které je důležité pro vložení těsnícího o-kroužku.
- [ ] celá konstrukce je zřejmě zbytečně masivní.

roman-dvorak, 2020-10-01:
> Plošný spoj se neopírá o přívodní konektor, ale je výše. Díky čemuž jej nelze dobře upevnit vůči vyústění trubiček

aha.. tohle jsem nepochopil správně.. takže teď bude konektor ještě výše.

kaklik, 2020-10-01:
Dnes jsem přigumičkoval snímač k nově vytištěné zmenšené variantě.

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

Tohle se stane, když do toho fouknu:

    0395; 2020-10-01T20:57:45.129444; Dp: +0.00 [Pa]; T: 32.774 [degC]; MAG_HDG: +63.04; SPD_W_DP: +0.00 [km/h]
    0396; 2020-10-01T20:57:45.183406; Dp: +0.00 [Pa]; T: 32.966 [degC]; MAG_HDG: +62.98; SPD_W_DP: +0.00 [km/h]
    0397; 2020-10-01T20:57:45.237408; Dp: +0.00 [Pa]; T: 33.110 [degC]; MAG_HDG: +62.77; SPD_W_DP: +0.00 [km/h]
    0398; 2020-10-01T20:57:45.291341; Dp: +0.00 [Pa]; T: 33.062 [degC]; MAG_HDG: +62.71; SPD_W_DP: +0.00 [km/h]
    0399; 2020-10-01T20:57:45.345361; Dp: -24.00 [Pa]; T: 33.062 [degC]; MAG_HDG: +62.59; SPD_W_DP: +1.76 [km/h]
    0400; 2020-10-01T20:57:45.399374; Dp: -34.15 [Pa]; T: 33.110 [degC]; MAG_HDG: +62.70; SPD_W_DP: +2.10 [km/h]
    0401; 2020-10-01T20:57:45.453341; Dp: -38.95 [Pa]; T: 33.062 [degC]; MAG_HDG: +62.50; SPD_W_DP: +2.25 [km/h]
    0402; 2020-10-01T20:57:45.507374; Dp: -55.35 [Pa]; T: 33.253 [degC]; MAG_HDG: +62.02; SPD_W_DP: +2.68 [km/h]
    0403; 2020-10-01T20:57:45.561325; Dp: -64.85 [Pa]; T: 33.157 [degC]; MAG_HDG: +61.83; SPD_W_DP: +2.90 [km/h]
    0404; 2020-10-01T20:57:45.615369; Dp: -65.85 [Pa]; T: 33.062 [degC]; MAG_HDG: +61.66; SPD_W_DP: +2.92 [km/h]
    0405; 2020-10-01T20:57:45.669336; Dp: -74.90 [Pa]; T: 33.062 [degC]; MAG_HDG: +61.41; SPD_W_DP: +3.12 [km/h]
    0406; 2020-10-01T20:57:45.723355; Dp: -94.05 [Pa]; T: 33.157 [degC]; MAG_HDG: +61.27; SPD_W_DP: +3.49 [km/h]
    0407; 2020-10-01T20:57:45.777320; Dp: -67.15 [Pa]; T: 33.062 [degC]; MAG_HDG: +61.31; SPD_W_DP: +2.95 [km/h]
    0408; 2020-10-01T20:57:45.831347; Dp: -75.90 [Pa]; T: 33.253 [degC]; MAG_HDG: +60.68; SPD_W_DP: +3.14 [km/h]
    0409; 2020-10-01T20:57:45.885315; Dp: -71.70 [Pa]; T: 33.110 [degC]; MAG_HDG: +60.26; SPD_W_DP: +3.05 [km/h]
    0410; 2020-10-01T20:57:45.939326; Dp: -86.30 [Pa]; T: 33.110 [degC]; MAG_HDG: +59.96; SPD_W_DP: +3.34 [km/h]
    0411; 2020-10-01T20:57:45.993290; Dp: -82.25 [Pa]; T: 33.110 [degC]; MAG_HDG: +60.01; SPD_W_DP: +3.26 [km/h]
    0412; 2020-10-01T20:57:46.047329; Dp: -58.25 [Pa]; T: 33.110 [degC]; MAG_HDG: +60.58; SPD_W_DP: +2.75 [km/h]
    0413; 2020-10-01T20:57:46.101322; Dp: -111.90 [Pa]; T: 33.110 [degC]; MAG_HDG: +60.22; SPD_W_DP: +3.81 [km/h]
    0414; 2020-10-01T20:57:46.155342; Dp: -115.60 [Pa]; T: 33.062 [degC]; MAG_HDG: +60.43; SPD_W_DP: +3.87 [km/h]
    0415; 2020-10-01T20:57:46.209296; Dp: -123.40 [Pa]; T: 33.110 [degC]; MAG_HDG: +60.19; SPD_W_DP: +4.00 [km/h]
    0416; 2020-10-01T20:57:46.263326; Dp: -103.10 [Pa]; T: 33.349 [degC]; MAG_HDG: +60.30; SPD_W_DP: +3.66 [km/h]
    0417; 2020-10-01T20:57:46.317298; Dp: -74.25 [Pa]; T: 33.110 [degC]; MAG_HDG: +60.11; SPD_W_DP: +3.10 [km/h]
    0418; 2020-10-01T20:57:46.371327; Dp: -96.85 [Pa]; T: 33.110 [degC]; MAG_HDG: +60.13; SPD_W_DP: +3.54 [km/h]
    0419; 2020-10-01T20:57:46.425293; Dp: -72.90 [Pa]; T: 33.110 [degC]; MAG_HDG: +60.21; SPD_W_DP: +3.07 [km/h]
    0420; 2020-10-01T20:57:46.479305; Dp: -80.70 [Pa]; T: 33.110 [degC]; MAG_HDG: +60.26; SPD_W_DP: +3.23 [km/h]
    0421; 2020-10-01T20:57:46.533287; Dp: -22.30 [Pa]; T: 33.110 [degC]; MAG_HDG: +60.34; SPD_W_DP: +1.70 [km/h]
    0422; 2020-10-01T20:57:46.587304; Dp: -0.40 [Pa]; T: 33.110 [degC]; MAG_HDG: +60.25; SPD_W_DP: +0.23 [km/h]
    0423; 2020-10-01T20:57:46.641271; Dp: -0.10 [Pa]; T: 33.110 [degC]; MAG_HDG: +60.66; SPD_W_DP: +0.11 [km/h]
    0424; 2020-10-01T20:57:46.695276; Dp: +0.00 [Pa]; T: 33.110 [degC]; MAG_HDG: +61.02; SPD_W_DP: +0.00 [km/h]
    0425; 2020-10-01T20:57:46.749256; Dp: +0.00 [Pa]; T: 33.445 [degC]; MAG_HDG: +61.12; SPD_W_DP: +0.00 [km/h]
    0426; 2020-10-01T20:57:46.803318; Dp: +0.05 [Pa]; T: 33.157 [degC]; MAG_HDG: +60.91; SPD_W_DP: -0.08 [km/h]
    0427; 2020-10-01T20:57:46.857261; Dp: +0.00 [Pa]; T: 33.157 [degC]; MAG_HDG: +60.97; SPD_W_DP: +0.00 [km/h]
    0428; 2020-10-01T20:57:46.911293; Dp: +0.05 [Pa]; T: 33.349 [degC]; MAG_HDG: +61.18; SPD_W_DP: -0.08 [km/h]
    0429; 2020-10-01T20:57:46.965244; Dp: +0.00 [Pa]; T: 33.253 [degC]; MAG_HDG: +61.27; SPD_W_DP: +0.00 [km/h]

To stejné jsem zkoušel i s variantou s NACA profilem

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

Když do ní fouknu tak to dopadne takhle
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
roman-dvorak, 2020-11-02:
# Testování venturiho poličky

Venturiho poličku jsem připevnil na střechu auta. Cca 60 cm nad střechu.
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

### Měření
Měření bylo provedeno pomocí [skriptu](https://github.com/ThunderFly-aerospace/TFASPDIMU01/blob/TFASPD01A/sw/TFASPD_logger.py). GPS byla připojena do Omnie s LTE/GPS přijímačem a připojena do GPSD. Externí anténa byla přimagnetovaná na střechu auta.

Každé měření bylo provedeno na jiné cestě v normálním provozu. Proto podmínky byly dost nedefinované. Tento den však nefoukalo. Cílem bylo jet určité úseky s pomocí tempomatu (tedy konstantní rychlostí).

### Legenda ke grafům

- První graf je graf groundspeed z GPS X naměřený tlak z differencionálního senzoru.

- Druhý graf zobrazuje průběh měření. Modrý graf (levý sloupec) je GPS v km/h, Světle červený graf (pravý sloupec) je rozdíl tlaku v Pa.

## NACA0040, d=20

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

## NACA0045, d=20

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

roman-dvorak, 2020-11-09:
Docela výhodné bude venturiho poličku montovat obráceně (PCB nahoře) a víčko implementovat do nejvyššího dílu pylonu. Polička bude k pylonu připevňena z horní strany pomocí dvojice šroubů. Tak, jak je to v poličce aktuálně implementováno.

Toto vylepšení souvisí s jinou montáží serv #70

JanKott, 2020-11-10:
Můžete mi prosím nakreslit jaká je požadovaná změna?

roman-dvorak, 2020-11-10:
Moje představa je cca taková:

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

Asi ani není nutné, aby to byl přesně NACA profil. Víčko bude na anemometru připevněno z horní strany. Dvojicí šroubů po stranách v přední části anemometru. Cílem je anemometr co nejvíce vysunout dopředu.

V co nejzadnější části, (kde to materiál dovolí) by měla být příčná díra skrz a v ní dvě kapsy na matky. o něco nopřeději (cca 5-10 mm) by měl být ďolík (odebraná polokoule) která bude sloužit k aretaci anemometr tak, aby nemohlo dojít k jeho rotaci okolo dvojice šroubů. Hloubka stačí cca 2 mm, průměr cca 3 mm.

Mezi poličkou a víčkem by bylo dobré mít nějaký rantl, který zamezí natečení vody do senzoru. Zároveň by bylo dobré, aby bylo možné senzor tisknout na bok. (tj. aby vrstva tisku odpovídala proudnicím skrze poličku) Aktuálně se to tiskne kolmo na proudnice (na odtokovou hranu)

Víčko jsem předpokládal, že se bude tisknout na náběžnou hranu.

kaklik, 2020-11-17:
Dneska jsem o tom mluvil s @JanKott. Zde v popisu není uvedeno, že ta dvojice šroubů, která víčko upevňuje by měla procházet rantlem, aby skrz šrouby nemohlo napršet přímo na elektroniku snímače.

Ten způsob tisku bych preferoval na bok a to zejména z důvodu, že na náběžnou, nebo odtokovou hranu se špatně tiskne. Vliv zoubků na aerodynamiku profilu bude pro tenhle případ myslím zanedbatelný.

roman-dvorak, 2020-11-25:
@JanKott, nějaký progress? :)

JanKott, 2020-11-26:
No progress at all :-/

JanKott, 2020-12-09:
Víčko je upravené dle požadavků.

JanKott, 2020-12-09:
Zavřený asi neni dobrý stav.. Předávám k otestování.

kaklik, 2020-12-25:
Jsou vytištěny a složeny snímače připravené k otestování.

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

slimonslimon, 2020-12-25:
Při příštím letu by měl startovat můj stroj osazen těmito 2 poličkami a pitotovou trubicí (opravenou po havarii). Airspeed bude měžen pitotovou trubicí, tlaky budou logovány.

kaklik, 2021-02-17:
Tohle issue mi přijde vlastně hotové, až na ne úplně jasně uzavřený software.

slimonslimon, 2021-02-18:
na což je issue tady (?): https://github.com/ThunderFly-aerospace/TFASPDIMU01/issues/3 tudíž navrhuji toto issue uzavřít.

roman-dvorak, 2021-02-18:
Z HW stránky tomu zase chybí víčko, které bude vypadat asi trochu jinak.

Dne čt 18. 2. 2021 9:37 uživatel slimonslimon <notifications@github.com>
napsal:

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

kaklik, 2021-02-18:
> Z HW stránky tomu zase chybí víčko, které bude vypadat asi trochu jinak.

Pokud píšeš, že k tomu chybí víčko a zároveň bude vypadat asi trochu jinak. Tak zřejmě máš nějakou představu o tom, jak to víčko má vypadat, což tu není popsaný. :)

kaklik, 2021-02-23:
Zde je potřeba ještě:

- [ ] zapracovat víčko airspeed senzoru držící PCB [TFASPDIMU](https://github.com/ThunderFly-aerospace/TFASPDIMU01)
- [ ] Vyřešit umístění TFRPM viz issue: https://github.com/ThunderFly-aerospace/TF-G2/issues/76

Nakonec si myslím, že by bylo potřeba dát TFRPM z vrchní strany, aby bylo možné zkontrolovat funkci RPM snímače na vírníku stojícím na zemi a nenastal stejný problém jako je popsaný v issue https://github.com/ThunderFly-aerospace/TF-G2/issues/76 kdy je LED vidět jen ze spodní strany.

Myslím že by to šlo udělat tak, že se TFASPDIMU dá pod TFRM tak, že oba PCB se budou dotýkat plochou stranou bez součástek. Přes ně by pak mohlo být přitažené víčko přišroubované samořeznými šrouby.

kaklik, 2021-09-03:
Nové uchycení senzoru i s jednoduchým víčkem na šrouby funguje docela dobře.

Closed 2021-09-03.

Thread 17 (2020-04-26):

Pokusit se o implementaci RPM senzoru

roman-dvorak, 2020-04-26:
Tohle by se mohlo vyřešit tak, že se sloupek s ložisky sníží o cca 5 mm a nasadí se na to taková obrácená mistička, která se bude otáčet s rotorem. Ve spodní části pak bude nějaký senzor.

Zde je otázka, jaký senzor to bude??
 * IR reflexní
 * IR brána
 * Hallova sonda

kaklik, 2020-04-26:
To je stejný problém jako tohle: https://github.com/ThunderFly-aerospace/force_balance/issues/7

kaklik, 2020-07-21:
Implementována IR brána.

Closed 2020-07-21.

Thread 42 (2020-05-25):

Vykreslování naměřených dat do mapových podkladů

roman-dvorak, 2020-05-25:
Pro některé druhy měření by bylo vhodné umět vykreslovat naměřené skalární hodnoty do mapy, tak aby bylo možné vytvořit 3D heatmapu měřené veličiny v závislosti na poloze.  Vykreslovat tato data by mělo být možné online (real-time) v průběhu letu tak i z logů v post processingu.

Real-time vykreslování lze použít pro kontrolu průběhu měření ale především pro následnou navigaci do zajímavého místa popřípadě jeho detailnějšího prozkoumání.

Není asi vhodné pro tento účel vytvářet vlastní SW, protože je to velmi komplexní problém. Bylo by tedy vhodné využít nějakého existujícího mapového frameworku, který s takovými daty umí zacházet.

Hlavní požadavky které máme jsou:

1. Vizuální atraktivita zobrazení (bude využíváno i pro marketingové prezentace)
2. Možnost připojení na realtime data  (MavLink, ROS/MAVROS,MQTT, ...).
3. Zobrazení bodových dat a jejich interpolace přes prostor (Inverse Distance Weighting (IDW))

Známé programy:
 * [OpenDronMap](https://www.opendronemap.org/)
 * [QGIS](https://qgis.org/en/site/about/index.html)
 * [NGV](http://ngv.norut.no/)
 * [Marble](https://marble.kde.org/)
 * [Kepler](https://kepler.gl)
 * [ArcGIS](https://cs.wikipedia.org/wiki/ArcGIS)
 * [STK12](https://www.agi.com/newstk) - komerční nástroj, který asi využívá NASA.
 * [Cesium](https://cesium.com/blog/industries/uav/)
 * FlightGear?
 * [ROS](https://www.youtube.com/watch?v=BDzufMACM2M)?
 * [ParaView](https://www.paraview.org/)

Ještě by bylo zajímavé projít [tento seznam](https://www.osgeo.org/projects) a podívat se, zda tam není něco vhodného. Zajímavě vypadá například [GrassGis](https://www.osgeo.org/projects/grass-gis/).

Vizualizační knihovny
 * [VisPy](http://vispy.org/)

Komerční řešení podobné problematiky
 * https://www.iatecps.com/soarability

Pro inspiraci:
 * [Vizualizace mraků](https://vimeo.com/156297434) - zřejmě pomocí nástroje [ParaView](https://www.paraview.org/)

kaklik, 2020-06-01:
Jako nejperspektivnější řešení se zatím jeví přihnutí některého z existujících příkladů nástroje Cesium:

- https://cesium.com/blog/2019/04/29/gpu-powered-wind/
- https://cesium.com/blog/2017/11/17/paragliding-logbook/
- https://cesium.com/blog/2018/05/08/activeflight/
- https://cesium.com/blog/2016/02/03/vega/

Části software které pro realizaci něčeho takového v Cesiu jsou potřeba:

- Datová pumpa z MavLink packetů
- Databáze pro dočasné uložení dat  (z ní se budou data zobrazovat a v případě webového prohlížení i obnovovat)
- Definice zobrazení a výpočet interpolovaných dat

Closed 2020-11-05.

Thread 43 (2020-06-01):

Změřit poláru vírniku

kaklik, 2020-06-01:
Vírníku by bylo potřeba [změřit poláru](http://www.airspace.cz/akademie/rocnik/2009/07/polara.php), abychom věděli při jaké rychlosti můžeme očekávat minimální opadání.

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

Potenciálním problémem celého takového měření je, že polára se může v průběhu letu měnit.  Podle aktuálních parametrů hustota vzduchu, ušpinění rotoru, a podobně.

Pro létání v termice by tak bylo výhodné, kdyby měřící aplikace uměla fungovat i jako MPPT traceker, který by optimální rychlost klouzání neustále hledal.

kaklik, 2021-06-26:
Tohle issue by zřejmě nyní, když vírník nepřechází do spirály, už mohlo být řešitelné. :)

kaklik, 2021-08-13:
Zjištění z https://github.com/ThunderFly-aerospace/PX4Firmware/issues/35 zřejmě usnadnilo možný způsob řešení.

kaklik, 2021-11-15:
K tomuhle je zřejmě potřeba funční "airspeed mód".
FYI @roman-dvorak

roman-dvorak, 2021-11-15:
Nevím, jestli by nebyl vhodnější nějaký automatický režim (např loiter) s variabilním airspeed.. Kdy by se pak našel konkrétní airspeed setpoint s minimálním příkonem. Zřejmě ale bude existovat více optimálních hodnot. Například optimální airspeed pro dosažení co největší doby  letu vs optimální airspeed pro největší délku trajektorie letu.

O to se snaží tady: https://github.com/PX4/PX4-Autopilot/pull/18605 Tahle implementace má bohužel 3 rychlostní režimy (AIRSPEED_MIN/TRIM/MAX) a neumožňuje plynulou změnu. (Tato úprava zároveň má zvětšit robustnost ve větru)

Nalezení optimální rychlosti by možná mělo být i předmětem auto-tunning algoritmů https://github.com/PX4/PX4-Autopilot/pull/18330.

kaklik, 2021-11-15:
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

Ten automatický režim souvisí s tím jakým způsobem se vypořádáme s větrem. Protože v loiter režimu bude potíž s tím že během úseků na té kružnici bude mít vítr různou rychlost a směr.
Myslím si tak, že pokud by to měl být automatický režim měření, tak by musel obsahovat rovné přelety ve směru proti větru.
V automatickém režimu letu na kružnici by to ale určitě šlo provozavat v kombinaci s motorem. Je to ale myslím jiný typ měření.

kaklik, 2022-01-13:
Myslím si, že tohle by bylo zřejmě nejlepší implementovat ve formě [Flight Task](https://docs.px4.io/master/en/concept/flight_tasks.html)  uvnitř nějakého vhodného režimu letu. Nejvhodnější mi aktuálně přijde "airspeed" pro hledání parametrů optimálních parametrů bezmotorového letu. A pak "hold" pro hledání optimálních parametrů motorového letu.

Zřejmě by asi bylo možné, aby tento "MPPT optimizer" běžel vlastně pořád.  Protože nyní se třeba s airspeed zachází tak, že se letí AIRSPEED_TRIM, dokud regulátor nenarazí na nějaké limity. Jako třeba menší než minimální ground speed.  Předpokládá se tak, že AIRSPEED_TRIM je konstanta po celou dobu letu a je neměnnou charakteristikou UAV, což ale prakticky není pravda.
Optimizer by pak mohl AIRSPEED_TRIM měnit buď dynamicky, nebo pokud je schopen získat nějaký odhad v průběhu letu beze změny AIRSPEED_TRIM, tak ji aspoň nastavit na optimálnější hodnotu pro příští let. (Podobně jako se zachází s parametrem ASPD_SCALE).

Obávám se ale, že tento problém nelze vyřešit bez znalosti i vertikální složky větru, která může kazit měření opadání, jak je již naznačeno výše.

kaklik, 2022-05-14:
Možná by tohle celé měření šlo nahradit automatickým odhadem některých parametrů TECS regulátoru, jako například FW_T_RLL2THR, nebo zavedením parametru Throttle_to_STE_rate tj. převrácenou hodnotu od [STE_rate_to_throttle](https://github.com/PX4/PX4-Autopilot/blob/3fe4c6e3f56d68417918454188a3f968c1e5ccd6/src/lib/tecs/TECS.cpp#L289), která se nyní určuje z konstant FW_T_SINK_MAX a FW_T_CLMB_MAX. Místo toho by zřejmě měla být vypočtena z dostupných výkonů během letu.
Takové údaje by asi umožňily porovnání úprav virníků mezi s sebou ve smyslu horší/lepší bez toho aby bylo nutné měřit celou poláru.

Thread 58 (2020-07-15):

Roztáčení rotoru namotaným provázkem

kaklik, 2020-07-15:
Rotorovou hlavu by bylo potřeba upravit tak, aby bylo možné rotor manuálně roztočit na vyšší otáčky.
K tomu by mohla posloužit změna, kdy by se rotor roztáčel provázkem namotaným okolo špulky na rotorové hlavě.

Jako  základ špulky lze použít současný kalíšek určený k měření otáček rotoru.  Ten však v současné konstrukci neumožňuje přenášet kroutivý moment na rotor.

Řešením zřejmě je kalíšek sjednotit se [spodním dílem šroubovaným na placku rotoru](https://github.com/ThunderFly-aerospace/TF-G2/blob/master/CAD/stl/888_4003.stl), který se s rotorem spojuje dvěma šrouby. Tyto šrouby by mohly být použity pro přenášení momentu na rotorové listy.

Kalíšek je tak zřejmě potřeba zesílit a připravit na něj otvor do kterého se vloží zpevněný konec špagátu (asi napuštěný sekundovým lepidlem). Zbytek špagátu se omotá kolem špulky.

Výsledkem je stav kdy stačí zatáhnout za konec provázku a rotor se tím roztočí. Po vytažení celé délky provázku by měl celý zůstat v ruce.

slimonslimon, 2020-07-28:
Testované řešení:
https://github.com/ThunderFly-aerospace/TF-G2/blob/master/CAD/png/printplate_888_4008.png

díky zužování špulky se velmi snadno dosáhne překřížení špagátku a jeho snadnému namotání, vystužený konec provázku dle mého soudu není potřeba. Momentálně se do špulky vejde cca 1.6m bílého provázku na vázání balíků.

V rámci úpravy dílu: https://github.com/ThunderFly-aerospace/TF-G2/blob/master/CAD/png/888_1012.png pro uchycení Ir brány dojde k maximalizaci špulky. Při roztáčení na autě na platformě je možné tahat dál, než rozpětí rukou, ale menší silou.

kaklik, 2020-08-03:
Je pravda, že v současném řešení lze snadno dosáhnout překřížení provázku, ale  je to postup který je poměrně nedefinovaný.
Proto se stále domnívám  že by byl lepší postup s vyztuženým koncem provázku, jako je například [použit zde.](https://www.youtube.com/watch?v=J7-8nUQytks)

Díl se špulkou by myslím chtělo upravit tak, aby průměr špulky byl zvětšený alespoň tolik, aby neinterferoval s otvory pro šrouby určenými ke stažení rotoru.  Tím navíc dojde ke snížení potřebné boční síly, takže by nemělo být potřebné rotor z boku tolik podpírat při tahání za provázek.

Dále by myslím značně pomohlo, pokud by před startem bylo možné namotaný provázek pojistit v nějakém zářezu, aby nemohlo dojít k jeho svévolnému rozmotání. Zde by se asi hodily dva symetrické zářezy na obvodu, jednak pak bude možné vybrat jeden z dvojice a potom touto úpravou nedojde k rozvážení rotorového domku.

Při konstrukci tohoto roztáčecího mechanismu, by myslím bylo potřeba počítat s délkou provázku, která je znatelně menší, než rozteč rozpažených rukou většiny populace. Protože je nutné tento roztáčecí mechanismus používat i v případě startu z ruky.   Prakticky tak jde o délku provázku maximálně 1m.

Celkově jsou potřeba tyto kroky:

- [ ] Zvětšení průměru špulky pod rotorem na průměr větší než je rozteč šroubů rotoru
- [ ] Vytvoření otvoru pro zastrčení zpevněného konce provázku
- [ ] Vytvoření háčku do kterého lze namotaný provázek zatáhnout, aby nedošlo k jeho rozmotání před startem

kaklik, 2020-10-26:
Navrhoval bych roztáčecí bubínek upravit do této podoby:

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

[Snímač otáček](https://github.com/ThunderFly-aerospace/TF-G2/issues/64) by pak nebyl z boku, ale ze spodní strany.
Na bubínku by byl závit, který by zajišťoval jednak to že provázek nejde na bubínek namotat v protisměru a pak by měl také zabránit vzájemnému zapletení závitů.

Předpokládám, že při roztáčení by se provázek z bubínku odvíjel ve smeru od horního okraje ke spodnímu.  Důvod k tomu je ten, že při nejvyšších otáčkách rotoru pak bude provázek nejvíce vzdálen od šroubů na kterých drží rotorové listy.

kaklik, 2020-12-25:
Model by ve spodní části zřejmě bylo možné odlehčit tak, že okolo matice, by byl vysoký kužel, jinde by materiál byl odebraný.

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

Taktéž je zřejmě možné matici zapustit až skrz tento díl. Odpadl by pak problém s centrováním otvoru při skládání rotoru.

kaklik, 2021-01-01:
Z posledních pokusů vyplývá, že by bylo vhodné, aby pylon, nebo rotorová hlava ve svojí vrchní části obsahovala "hrazdu" přes kterou se přetáhne provázek namotaný na bubínek rotoru.
Důsledkem by mělo být, že k roztočení rotoru by stačil tah za provázek především směrem dolů. Nebyl by tak nutný druhý člověk, který nyní tahá za provázek a drží rotorový pylon, aby jej nevyvrátil do boku.

Hrazda by mohla být tvořena i bezzávitovou hladkou částí šnoubu. Ve složitější implementaci by byla lepší kladka s kuličkovým ložiskem. Výhodou použití ložiska s drážkovanou kladkou by bylo, že vydrží i mírný nesouosý tah bez snížení účinnosti.

slimonslimon, 2021-01-01:
případně by to mohla být celá soustava kladek k tažnému motoru, který by měl zařízení na tahání provázku v podobě dvou bubínků stlačených k sobě, takže by start vypadal tak, že by se přidáním plynu v prví fázy roztočil rotor předmotaným provázkem a pak už by se jen vírník vypustil z ruky

kaklik, 2021-01-01:
To s těmi dvěma bubínky nechápu, ale nápad je to zajímavý.  Akorát na tom tahání za provázek rukou se mi líbí že provázek pak zůstane na zemi a vírník ho netahá s sebou.

slimonslimon, 2021-01-01:
něco jako extruder v tiskárně, akorát místo filametu provázek a kapánek vyšší otáčky

kaklik, 2021-01-02:
> něco jako pohon filamentu v tiskárně, akorát kapánek vyšší otáčky

Aha! už to zřejmě chápu. Tím chceš vyřešit to, aby se provázek nenamotával na nějakou špulku u motoru, ale aby propadl na zem. No takovéhle řešení mě nenapadlo. :) Je to ale zajímavé protože takové řešení by mohlo vyřešit potíž s tvrdým rozběhem na začátku tím, že provázek mezi kolečky proklouzne.

slimonslimon, 2021-01-02:
Kdyby se tím chtěl někdo zabývat, tak je to takový hezký ucelený úkol - vzít rotor s měřákem otáček a tažný motor a zkusit někde "na stole" (v bunkru) roztahovat rotor tažným motorem... Já na to zrovna čas nemám :-(

kaklik, 2021-01-02:
> Kdyby se tím chtěl někdo zabývat, tak je to takový hezký ucelený úkol - vzít rotor s měřákem otáček a tažný motor a zkusit někde "na stole" (v bunkru) roztahovat rotor tažným motorem... Já na to zrovna čas nemám :-(

První krok podle mě stále je,  vyladit vůbec to roztáčení rotoru provázkem, tak aby to bylo bezchybný.  Pak se dá uvažovat o nějakém pohonu motorem. U motoru ale vidím výhodu, že ten provázek zřejmě může být i celkem dlouhý. :)

kaklik, 2021-01-18:
Aktuální provedení rotorové hlavy s provázkovou prerotací vypadá takhle:

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

Provedení by mělo být kompatibilní s aktuálně používanou konstrukcí rotorové hlavy.

kaklik, 2021-02-08:
Při tisku jsem zjistil, že:

- [ ] Výšku bubínku je potřeba o cca 1mm zkrátit, aby nedocházelo k drhnutí o spodní část rotorové hlavy
- [ ]  Horní šestihran pro plastovou matici šroubu udělat průchozí až ven, aby nebyla zbytečně využitá tak velká délka šroubu.

kaklik, 2021-05-03:
Řešení bylo otestováno na aerodynamické váze a zřejmě je funkční.

Closed 2021-05-03.

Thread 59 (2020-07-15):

Zvětšení rozlišení RPM senzoru

kaklik, 2020-07-15:
[Aktuální kalíšek](https://github.com/ThunderFly-aerospace/TF-G2/blob/master/CAD/stl/printplate_888_1014.stl), který slouží k měření otáček rotoru, má pouze 4 díry.
Takový počet děr je dostatečný pro měření otáček jednou za sekundu.  Z experimentů ale vyplývá, že je potřeba otáčky snímat minimálně 4x za sekundu. Z čehož by při zachování rozlišení vyplýval počet děr alespoň 16.

Úprava kalíšku na takto zvetšený počet děr je reálná i při zachování současného průměru.  Myslím si však, že průměr kalíšku je potřeba trochu zvětšit. (Pro zachování kompatibility se současným umístěním optické brány by ideální zvětšení bylo asi o 1mm průměru)
Je to důležité ze dvou důvodů. Jednak proto aby se do něj snáze vešla optická závora. Druhý důvod je, že kalíšek je pravděpodobně potřeba upravit tak, aby [umožňoval roztočení rotoru kusem špagátu](https://github.com/ThunderFly-aerospace/TF-G2/issues/58).

roman-dvorak, 2020-07-15:
Pro použití pro roztáčení rotoru (#58) by to chtělo celkově změnit konstrukci tohoto dílu. Problém tohoto dílu je, že oproti ose rotoru drží za velmi malou plochu a při roztáčení za provázek by se to začalo velmi snadno protáčet. Řešení tohoto problému je několik.

Aktuální verze má opravené dření o optický senzor a zvětšen počet děr na 16.

kaklik, 2020-07-15:
@slimonslimon  To vypadá, že tohle issue související s #58 je vyřešeno..

kaklik, 2020-07-28:
Řešení bylo otestováno společně s úpravou pro roztáčení rotoru  a je funkční pro otáčky rotoru do ~2000 RPM,

Closed 2020-07-28.

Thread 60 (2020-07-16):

Úprava rotorových podložek

kaklik, 2020-07-16:
Rotorové podložky je potřeba upravit tak, aby obrysem seděly k nové rotorové placce #57.

Díly [888_4005](https://github.com/ThunderFly-aerospace/TF-G2/blob/master/CAD/stl/888_4005.stl), [888_4004](https://github.com/ThunderFly-aerospace/TF-G2/blob/master/CAD/stl/888_4004.stl)  a [888_4006](https://github.com/ThunderFly-aerospace/TF-G2/blob/master/CAD/stl/888_4006.stl) je potřeba tak, aby lícovaly ze spodní i horní strany s novou rotorovou destičkou [888_4002](https://github.com/ThunderFly-aerospace/TF-G2/blob/master/CAD/stl/888_4002.stl)
Cílem tak je, aby rotorová destička byla sevřena mezi ostatní díly v celé svojí ploše.

Aktuální nekompatibilita je vidět na následujících dvou obrázcích ze sestavy [888_4101](https://github.com/ThunderFly-aerospace/TF-G2/blob/master/CAD/src/drawings/888_4101.scad)

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

cesilko1, 2020-07-16:
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

kaklik, 2020-08-18:
Momentálně je tohle issue vyřešeno dočasně tím že podložky jsou stále tvořeny polygonem, který ale v důsledku zřejmě není parametrický.

To znamená, že například nelze:

- Nastavit mezeru v podložkách pro konkrétní úhel prověšení listů před startem
- Rozteče šroubů a pozice jsou pravděpodobně momentálně dány číselnými hodnotami v kódu, těžko se tak díly provazují vzájemně, nebo vytváří závislosti na dalších rozměrech.

kaklik, 2021-08-04:
Tohle bych zatím navrhoval neřešit a počkat jak dopadne free-flapping-rotor od @slimonslimon

kaklik, 2021-08-21:
Výsledkem úspěšného testu free-flapping rotoru je, že není potřeba tento úkol dále řešit.

Closed 2021-08-21.

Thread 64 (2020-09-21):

Aktualizace snímače otáček rotoru

kaklik, 2020-09-21:
## TODO:
 - [X] Vyřešení umístění pcb TFPROBE do spodního dílu rotorové hlavy
 - [ ] Zarážka pro správné zastrčení PCB do dílu
 - [x] Zastínění reflexního senzoru, aby nemohl být snadno osvícen ze zadní strany
 - [x] Zvětšení tloušťky a eliminace děr ve stěnách bubínku, aby nemohlo dojít k prosvícení
 - [x] Vyřešení otvoru v horní sploštělé části
 - [x] Kapsa na samojistnou matku pro uchycení táhel serv.

<hr>

[Aktuální snímač otáček](https://github.com/ThunderFly-aerospace/TFRPM01) je použit v kombinaci s optickou závorou.
Na TFRPM01B je přidán pull-up ?3k? a fototranzistor je připojený na stejný vstup jako se připojuje hallova sonda.

Použitá optická závora je náhodného typu ze zásob Robozoru. Je připevněna na vertikální držák ložisek rotorové osy. Skrz závoru se otáčí kalíšek s děrovanými otvory.

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

Lepší řešení by zřejmě bylo upravit současnou kontrukci TFRPM01B, tak aby na PCB byla zároveň optozávora i hallova sonda.
Tím by byla odststraněna nutnost připojení externího snímače.

Celé PCB by pak mohlo být horizontálně [mezi rameny táhel](https://github.com/ThunderFly-aerospace/TF-G2/blob/master/CAD/stl/888_1012.stl) k servům rotorové hlavy. Dolů z rotorové hlavy by tak vedl pouze čtyřžilovýkablík k I2C.

kaklik, 2020-10-26:
V případě že by pro snímání otáček, byl použit reflexivní snímač, tak existují dva způsoby jeho použití.

### Snímač umístěný rovnoběžně se směrem otáčení

V této pozici je vysílač a přijímač reflexivního snímače umístěn podélně se směrem rotace.  Což odpovídá následujícímu obrázku. Pohled na rotorovou hlavu ze zadní strany, kde plošný spoj se snímačem je uchycen mezi rameny táhel rotorové hlavy.

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

### Snímač umístěný radiálně

V tomto umístění by vysílač a přijímač reflexního snímače byly orientovány v radiálním směru vůči ose rotace rotoru.
Umístění je ilustrováno na následujícím obrázku, který reprezentuje pohled z boku na rotorovou hlavu.

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

V obou případech je reflexivita bubínku zajištěna spodní plochou bubínku, která při tisku bude položena na tiskové podložce.
V této ploše jsou tmavé otvory realizované dutinou, která může přecházet v celý objem bubínku. Na obrázcích výše jsou znázorněny příčky, které mají sloužit ke zpevnění bubínku vůči ose rotace.

kaklik, 2020-10-26:
@roman-dvorak
Tohle vypadá na to, že repozitář vůbec neobsahuje reálně použitou verzi měřícího děrovaného bubínku rotoru.

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

kaklik, 2020-11-21:
Zatím jsem vytvořil přípravu pro uchycení TFPROBE.

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

roman-dvorak, 2020-11-24:
@kaklik ... Jak se sem strká ta matka? :D

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

Navrhoval bych vytvořit kapsu.

roman-dvorak, 2020-11-24:
Při doražení PCB do konce, drážky PCB naráží na šroub. Děje se tak i v případě, že pod hlavou šroubu není podložka.

Bylo by dobré, aby v drážce byla zarážka, která by definovala maximální zastrčení PCB bez toho, aby to naráželo do šroubu roll osy rotorové hlavy.

kaklik, 2020-11-25:
Já úplně nemám nápad, jak zajistit, aby šlo rozmontovat Roll osu a přitom tam mohl zůstat ten PCB.  Předpokládal jsem že se ten PCB bude muset vyndavat. Protože při montáži tam dost vadí hřebínek který trčí dolů, jednoduché posunutí PCB výše proto moc nepomůže.

Co se týká řešení té lámací hlavy, tak jsem přemýšlel o rozdělení tohoto dilu na dva díly, které by se šroubovaly k sobě.  Tím by se po odlomení teoretecky nemusela odšroubovávat táhla k servům.

S tím vkládáním matice šroubu je to blbý, ale nejsem si jistej, zda je možné v kombinaci s kapsou používat samojistnou matici.

roman-dvorak, 2020-11-25:
> Já úplně nemám nápad, jak zajistit, aby šlo rozmontovat Roll osu a přitom tam mohl zůstat ten PCB. Předpokládal jsem že se ten PCB bude muset vyndavat. Protože při montáži tam dost vadí hřebínek který trčí dolů, jednoduché posunutí PCB výše proto moc nepomůže.

OK, neřešme to. Vyndat PCB není složité :)

> Co se týká řešení té lámací hlavy, tak jsem přemýšlel o rozdělení tohoto dilu na dva díly, které by se šroubovaly k sobě. Tím by se po odlomení teoretecky nemusela odšroubovávat táhla k servům.
Jo, tohle je fajn nápad! Mělo by to být součástí #69

> S tím vkládáním matice šroubu je to blbý, ale nejsem si jistej, zda je možné v kombinaci s kapsou používat samojistnou matici.
Navrhoval bych to zkusit. Protože jsem dneska zkoušel tu matku tam vložit a je to opravdu složité.

>Při doražení PCB do konce drážky, PCB naráží na šroub. Děje se tak i v případě, že pod hlavou šroubu není podložka.
Tento problém nebude nastávat, protože PCB stejně nebude tak hluboko v dílu.

kaklik, 2020-12-24:
Upravený bubínek s vnitřními zuby pro snímání otáček rotoru [TFRPM01B](https://github.com/ThunderFly-aerospace/TFRPM01) v kmbinaci s [TFPROBE](https://github.com/ThunderFly-aerospace/TFPROBE01).

https://user-images.githubusercontent.com/1194177/103105607-1edae000-462f-11eb-8e46-ee450d7dc4fb.mp4

kaklik, 2020-12-25:
Ta zarážka na PCB TFPROBE momentálně postrádá význam, protože PCB musí být zaražený v drážce až k hlavě šroubu, aby to fungovalo správně..

kaklik, 2021-01-17:
Poslední iterace vypadá takto:

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

Myslím, že řešení je již použitelné.  Další zlepšení je možné až po dalších úpravách jako je #69.

Řešení je nyní kompatibilní s původní rotorovou hlavou TF-G2  @slimonslimon.

kaklik, 2021-02-19:
Čidlo po posledních úpravách funguje i těsně vedle 60W žárovky. Test na přímém slunečním světle je potřeba ještě provést, ale domnívám se, že problém je vyřešen.

kaklik, 2021-03-27:
Na základě poznatků z issue: https://github.com/ThunderFly-aerospace/TFRPM01/issues/10 to vypadá, že je potřeba zvýšit barevný kontrast měřícího kloboučku.

Jedna z možností, jak to vyřešit je vzít nějaký "IR tmavý" materiál. Například modrou, nebo šedou a na kloboučku vytištěném z této barvy obarvit pouze měřící zuby bílou fixou.

kaklik, 2021-03-28:
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

roman-dvorak, 2021-03-28:
Skvělé.. tohle vypadá, že půjde realizovat relativně snadno.

kaklik, 2021-03-28:
U modrého kloboučku je situace o něco horší, kvůli nižší hodnotě maximální hodnoty napětí.  To je na hranici funkčnosti, těsně pod hodnotou 2V. Tuto situaci by bylo možné zlepšit snížením hodnoty pull-upů buď na TFPROBE, nebo na TFRPM.

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

Nicméně i při současném nastavení, snímač ještě stále měří.  Jak je z grafu vidět, tak vysoká hodnota má trochu rozptyl, závislý na přesné poloze kloboučku. To je zřejmě způsobeno tím, že je měření provedeno na starší verzi kloboučku, která ještě nemá tak přesně umístěné zuby.  Je pravděpodobné, že s novou verzí by byl signál lepší.

kaklik, 2021-04-08:
Vyzkoušel jsem ještě novou tvarovou úpravu kloboučku, která má eliminovat výše popsanou nedokonalost způsobenou vyosením zubů. V podstatě to zřejmě zlepšuje, ale ne výrazně.

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

Způsob snímání ale pokládám za funkční.

Closed 2021-04-08.

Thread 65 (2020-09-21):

Pohonné ústojí vírníku

roman-dvorak, 2020-09-21:
Pro opakovatelnost výroby vírníků TF-G2 (TF-G3) je potřeba vybrat spolehlivé a dostupné ESC regulátory, motory a vrtule.

#  ESC

- [x] Vybrané ESC:

Na regulátory jsou požadavky
 * Telemtrická data přes UAVCAN
 * Dostupnost
 * Výkon ~50A (@ 3S)
 * OpenSource (výhoda, pokud ne tak reálná měření)
 *

## [Myxa](https://zubax.com/products/myxa)
Regulátor Myxa od Zubaxu.

Klady
* Odpovídající výkon
* UAVCAN (plná podpora včetně nastavování přes CAN)
* Malý rozměr, malá hmotnost
* Zubax vypadá jako docela komunikující firma, aktivní vývoj
* OpenSource, několik variant
* Podpora PPM + UAVCAN ovládání

Zápory
* Vyžaduje 4S akmumulátor
* Nemá BEC

# Motor
- [x] Vybraný motor:

Požadavky:
 *

# Vrtule
- [ ] Vybraná vrtule:

Požadavky:
 * Známé parametry
 * Dostupnost
 * Cena (spotřební materiál)

Jako součást s nejmenší možností výběru je je asi regulátor. Při volbě Myxi jsme omezeni především na to, že nejnižší podporované napětí splňuje 4S akmululátor. Od toho se odvíjí výběr zbylých komponent.

roman-dvorak, 2021-06-26:
Po několika pokusech se ukazuje, že MYXA pro TF-G2 (4S) dostačuje ale s nevelkou výkonostni rezervou.

Stále tedy v úvahu připadá používání VESC regulátoru. Na motorové váze bude vhodné tyto dva regulátory porovnat a případně se pokusit myxu nějakým způsobem lépe nastavit.

kaklik, 2021-07-06:
Nevím sice na jakém konektoru je u [nového VESC](https://www.neven.cz/kategorie/elektronicke-soucastky/stmivace/pwm-regulator-otacek/regulator-vesc-bldc-superfoc6-8-50a-esc/) RC PWM vstup. Nicméně jsem zjistil, že zřejmě nemáme sedmipinový konektor.  Není tak možné jeden z konektorů na PCB použít. Konektory, ke kterým máme protikusy jsou vyfoceny na následujícím obrázku.

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

kaklik, 2021-09-04:
Tohle issue je zřejmě potřeba rozebrat na dílčí části, které je nutné řešit samostatně.

Closed 2021-09-04.

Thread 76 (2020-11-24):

Zlepšit umístění TFRPM pcb

roman-dvorak, 2020-11-24:
Bylo by dobré, do poličky uprosřed pilonu vylepšit připevňení senzoru tak, aby matka v něm byla zapuštěná (tj. aby nebyl potřeba klíček a umístit ho více do středu tak, aby hrana PCB nekolidovala s bočnicemi pylonu.

Zároveň by nebyla špatná nějaká krabička, která by to zakrytovala před vodou. Zároveň je potřeba vyřešit nějaké svedení všech kabelů z rotorové hlavy.

- [ ] zlepšit viditelnost TFRPM indikační LED. Aktuálně je na poličce vidět na denním světle akorát zespodu a to ještě mizerně.

kaklik, 2020-11-25:
Asi bych potřeboval nějaký obrázek, abych pochopil, co tohle issue znamená.

roman-dvorak, 2020-12-02:
Původně to bylo myšleno tak, že se přesune senzor do prostoru střední příčky pylonu, kde se na něj vytvoří nějaký "držák".

Nyní bych navrhoval TFRPM dát někam do spodní části vírníku (někam do prostoru ESC a autopilota). Pro začátek asi v TFRPM01 v krabičče, ve které je dodávaný.

Tohle z důvodu, že RPM kablík se snadno vytrhne z rotorové hlavy (z TFPROBE) a nebude se tahat za I2C vedení při možné nehodě.

kaklik, 2021-02-17:
A jak to teď vlastně je s použitím TFRPM driveru na stejné sběrnici jako TFSLOT?  Funguje to, nebo ne?

Protože k TFSLOT se stejně I2C na pylon bude tahat, takže nevidím moc rozdíl v tom tam vést dvakrát I2C, nebo I2C a servokablík.

Z hlediska HW by bylo nejlepší řešení jen jedno I2C na které by byly připojeny oba senzory, díky tomu, že TFRPM je průchozí.  Vím ale že dříve jsme s tímto řešením měli potíže. Je tak otázka zda je to však relevantní i pro současný software?

slimonslimon, 2021-02-18:
Tady asi chybí nějaké "měření/pokusy" který by zjisti, kde je problém.

Driver neprovádí novou inicializaci RPM senzoru. Ale je potřeba vyzkoušet že reset rpm driveru stačí na obnovení funkčnosti.

roman-dvorak, 2021-02-23:
Na vírníku 4S tohle bude TFRPM integroaný do blízkosti TFSLOT. Proto je toto issue již nerelevantní.

kaklik, 2021-03-22:
Issue lze zavřít, až když bude reálně vyřešené.

kaklik, 2021-04-02:
> Tady asi chybí nějaké "měření/pokusy" který by zjisti, kde je problém.
>
> Driver neprovádí novou inicializaci RPM senzoru. Ale je potřeba vyzkoušet že reset rpm driveru stačí na obnovení funkčnosti.

Z [tohoto experimentu](https://github.com/ThunderFly-aerospace/TF-G2/issues/88#issuecomment-785433829) vyplynulo, že snímače na jedné sběrnici fungují a čtení nepadá. Co ale nefunguje je měření otáček, které při takovém zapojení občas dává zápornou hodnotu otáček..

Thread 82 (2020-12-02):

Zlepšená konstrukce pylonu a rotorové hlavy

roman-dvorak, 2020-12-02:
- [x] Spodní rámeček 888_1007
 - [x] Spodní část držáku silentbloků 888_1008
 - [x] Vybrat + otestovat správné silentbloky
 - [x] Horní část držáku silentbloků
 - [x] Implementace Airspeed #16
 - [x] Umístění serv #70
 - [x] Rotorová hlava
 - [x]  #69

<hr>

Protože doposud nedošlo k výrobě vírníku v podobě frézovaných (nebo laserem pálených) dílů, tak bych odstoupil od tohoto způsobu výroby. Trochu bych se inspiroval tyčovým pylonem na TF-G1.

Uprostřed kostry vírníku by byl rámeček, který bude zpevňovat trup a bude pevným základem pylonu. V něm by byly 4 uhlíkové tyčky průměru 6 nebo 7 mm (jako jsou aktuálně na platformě). Ty povedou do druhého rámečku. V rámečcích budou zalepeny. Skládání bude probíhat tak, že se tyčky prostrčí ze spodní strany do horního rámečku. Tím bude skládání snazší než u pylonu TF-G1.

Do horního rámečku budou zašroubovány 4 silentbloky, které budou fungovat jako odpružení/odvibrování pylonu. Ovládací prvky budou z důvodu tuhosti řízení v horní části rotorové hlavy.

Horní část ještě nemám přesně promyšlenou. Ale mělo by to vypadat tak, že bude co nejnižší a nejkompaktnější. Stále se počítá s uspořádáním serv na boku. Protože to snižuje podélnou plochu pylonu a zároveň tuhost řízení. V této části bude také airspeed senzor, který může být nyní širší tak, jak potřebujeme (@JanKott #16).

Také jsem přemýšlel o rotorové hlavě založené na kulovém čepu. Ale s tím si nejsem jistý.

Další otázka je implementace trhacího pylonu. Nabízí se několik řešení. Nejvíce se mi líbí, že by se vytrhly silentbloky v nějakém definovaném - oslabeném místě. (I tak se rotor má prioritně  trhat v listech #75 popř. domku ložisek rotoru #69 :smile: )

Očekával bych, že by se těmito změnami zvětšila pevnost celé konstrukce.

kaklik, 2021-07-05:
Tak mám teď po montáži nových zařízení na střechu měřícího auta a zároveň z průběhu testů tomu několik domnívám se zásadních poznatků.

1. Vypadá to, že aerodynamický odpor na střeše auta zvětšují zejména kabely, tedy tenké objekty v malém kruhovém průřezu zasahující do proudu vzduchu. Je to sice poměrně neexaktní měření, ale změna je po přidání kabelů myslím i slyšitelná.
2. Zdá se že realizace vícetyčkového pylonu s tyčkami malého průřezu není dobře realizovatelná. Protože je problém s rozkladem sil do větší plochy modelu z tenké uhlíkové tyčky. Tento problém by zřejmě bylo možné vyřešit, ale už i dosud vynaložené úsilí je nemalé.
3. Kvůli budoucí změně konstrukce ocasní plochy by bylo výhodné, kdyby existovala středová tyčka pod pylonem na kterou by bylo možné uchytit otočnou směrovku umístěnou pod rotorem. Tato úvaha vede k redukci počtu stojin v pylonu ze čtyř na tři.

Kvůli výše zmíněným bodům bych proto navrhoval konstrukci pylonu změnit na jednotrubkovou verzi. :) Vím že podobné řešení měl i původní TF-G1. V jehož případě vznikal problém zejména s použitím prerotátoru a s pevností spoje mezi vertikální stojinou a podélnou osou trupu.
Domnívám se, že u malé verze TF-G2 by tyto potíže vznikat nemusely. Neboť nemá prerotátor a spoj mezi vertikálním pylonem a trupem je stejně realizován silentbloky, což je řešení, které by myslím bylo vhodné zachovat.

Potřebná změna by tak byla pouze v úpravě spodního montážního rámečku pro pylon tak, aby obsahoval kříž do jehož středu by bylo možné vertikální pylon uchytit. Nahoře u rotorové hlavy by trubka mohla být vetknuta do nejtlustšího místa TFSLOT.

Toto nové řešení by mohlo mít výhodu i ve snazším utěsnění pláště vírníku proti vodě. Neboť na jednoduché vertikální trubce, může být posuvný díl utěsněný o-kroužkem, kterým se přikryje otvor v textilním plášti vírníku.

Další potenciální výhodou by pak mohla být možnost vedení kabeláže uvnitř trubky. To by mohlo být významné zejména v situaci, kdy by se použila trubka o průměru 13mm, která by měla být dostatečná pro prostrčení prodlužováku servokabelu.

kaklik, 2021-07-06:
K vedení kabeláže z pylonu existuje ještě alternativní možnost na trubku vytvořit nacvakávací 3D tištěný kryt s tvarem NACA profilu, kterým budou kabely svedeny do prostoru trupu.

kaklik, 2021-07-15:
@roman-dvorak  udělal úpravu konstrukce pylonu rotorové hlavy, která pravděpodobně všechny zmíněné potíže řeší.

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

Hlavním zádrhelem tak je nedokončená realizace vyměnitelného dílu lámací rotorové hlavy #69

kaklik, 2021-07-30:
S novou konstrukcí pylonu bylo již provedeno několik letů bez zjevných nedostatků.

Closed 2021-07-30.

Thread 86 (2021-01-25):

Uchycení podvozkových nohou

kaklik, 2021-01-25:
[Aktuální sestava](https://github.com/ThunderFly-aerospace/TF-G2/blob/4s/CAD/src/assembly/full_assembly.scad) v místě, kde mají být uchycené podvozkové nohy vypadá takto:

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

Protože podvozková noha je část, která se bude pravděpodobně i v budoucnu poměrně často měnit, tak je zřejmě vhodné její uchycení konstruovat tak, aby byla snadno vyměnitelná.

### Přechodový díl pro uchycení podvozkové nohy

Z toho mi vyplývá že by neměla být uchycena na pouzdro akumulátorů jak bylo původně v plánu, ale v místě kolmého spoje bočnice a spodní podložky.  Protože bočnice i podložka v tomto místě snadno praskají, tak je nutné oba díly vyztužit.
Důvody proč podvozek nemít uchycený na pouzdro akumulátorů jsou následující:

- Při sundání pouzdra akumulátoru by nebylo na co vírník položit
- Všechny síly z podvozku přenášely přes pouzdro akumulátoru, což může zbytečné vést k jeho zbytečnému poškození
- K udržení rozchodu by muselo být rozšíření provedeno délkou podvozkové nohy, což je nevýhodné, protože tenká podvozková noha je už nyní náchylná na ukroucení a její horizontální prodloužení by tuto situaci jen zhoršilo.

Toho lze dosáhnout konstrukcí nového dílu, který bude přišroubován k bočnicím, tak že vyztuží spoj bočnice a podložky.  K tomuto dílu bude teprve šroubována podvozková noha.

Benefity tohoto řešení jsou:
-  Není nutné, aby podvozková noha měla rastr děr přesně shodný s rastrem bočnic
-  Fakt že montážní adaptér podvozkové nohy bude šroubován k bočnici lze využít k zajištění matice pro podvozkovou nohu proti bočnici tak, že není možné, aby po odšroubování podvozkové nohy matice vypadla
-  Adaptér může na straně podvozkové nohy končit rovnou plochu, není tak nutné, aby podvozková noha měla levou nebo pravou variantu
- Tvarem adaptéru lze jednoznačně definovat umístění podvozkové nohy na bočnici a nemůže tak dojít k montážnímu omylu.

kaklik, 2021-02-17:
Uchycení podvozkových nohou bude zřejmě potřeba nějak upravit i v místě připojení k trupu. Neboť je to aktuálně nejcitlivější část podvozkové nohy, která je náchylná na poškození.

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

kaklik, 2021-02-22:
K ukrucujícím se podvozkovým nohám mám následující návrh jak to vyřešit:

Stačí ty odlehčovací trojuhelníky  na začátku udělat menší a začít je zmenšovat až třeba v 1/3 délky té nohy. Tím vznikne u kořene té nohy délka, kde se bude postupně ztenčovat ten materiál, protože noha se bude zužovat ale trojúhelníky budou nejdřív chvíli stejný (menší než jsou teď).

Respektive stačí, aby zmenšování trojúhelníků mělo trochu jiný spád, než je zužování nohy. Tím vznikne u kořene nohy více materiálu, který bude schopen přenášet zvýšené zatížení vznikající na páce nohy.

Aktuální řešení totiž obsahuje problém, že zatížení podvozkové nohy směrem ke kořenu roste, ale neroste průřez materiálu, přes který se síla může přenášet.

kaklik, 2021-05-03:
Aktuální úprava zřejmě řeší potíž s ukrucováním nohy popsané v komentáři výše.

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

Zbývá tak návrh nového dílu, který umožní napojení na trup.

kaklik, 2021-05-11:
> Ještě by mi přišlo lepší pro tisk, kdyby ta základna trojúhelníků byla v rovině se zůžením nohy.

Ano, souhlasím, na to je separátní issue, které zatím nikdo neřeší https://github.com/ThunderFly-aerospace/TF-G2/issues/98

>
> Ještě mě napadlo, co zkusit nějaký takovýhle nástroj na analýzu problému lámání nohou: https://youtu.be/7pKvMlo5aMw
> Já si totiž myslím, že by tam uvnitř měla být přenosová výstuha.

Nemyslím si, že je nyní přímo problém v té konstrukci podvozkové nohy. Ale takovýhle nástroj by mohl být užitečný i pro jiné díly. Problémem u 3D tisku je ale to, že ten tištěný model není homogenní, takže to nelze počítat s izotropními tenzory.  Možná to ale jde nějak vyřešit, nezkoušeli jsme to.

V případě podvozkových nohou je ale nyní myslím problém hlavně v tom vůbec mít nakreslené všechny díly. Druhý problém je pak jejich správné dimenzování, ale to už lze udělat metodou pokus-omyl.

kaklik, 2021-05-17:
@roman-dvorak udělal provizorní úpravu pro montáž podvozkové nohy, která ale moc nezohledňuje zdejší původní plán.

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

Nicméně zřejmě umožní dočasnou montáž aktuálně navržených podvozkových nohou.

kaklik, 2021-05-18:
Řešení, které bych navrhoval si představuji nějak takhle:

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

Z boku by vypadalo přibližně takto:

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

Jde o to, že šrouby nohy nebudou pokračovat skrz bočnici, ale budou posunuté oproti původnímu rastru na bočnici.  Všechny šrouby přitom mohou být klidně utopené, neboť adaptér (888_2004) může být dostatečně tlustý na to aby to bylo možné.

kittlerm, 2021-05-18:
Problem trochu je, podstavec pro nohu přesahuje tu rozteč bočnice, takže buď jsou šrouby pro nohy ve vzduchu nahoře nebo dole:
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

kittlerm, 2021-05-19:
Tak to mam asi hotove (ackoli je to cunada, kopiruje to celou 1003), akorat vymyslet umisteni:
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

roman-dvorak, 2021-05-19:
Aby to šlo takto použít, tak tam bude potřeba přidat nějaké tolerance okolo té drážky na  bočnice.

kittlerm, 2021-05-19:
> Aby to šlo takto použít, tak tam bude potřeba přidat nějaké tolerance okolo té drážky na bočnice.

jj taky jsem si rikal, i na ty ostatni diry na kryt, dnes to zkusmo vytisknu a kouknu na to.

kittlerm, 2021-05-19:
Mám ale větší problém, že se neobjevil nový gcode v gcodes repu https://github.com/ThunderFly-aerospace/gcodes/blob/TF-G2/refs/heads/mini/edee/gcode/TF-G2_printplate_888_2004.gcode

kittlerm, 2021-05-19:
> Aby to šlo takto použít, tak tam bude potřeba přidat nějaké tolerance okolo té drážky na bočnice.

Nakonec ten okraj zvětšovat ani není třeba:
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

Ale už to mam připravené, jen musím ještě doladit výšku, protože M3x12 je málo a M3x14 je moc a nevejde se, následně dochází k odtažení od bočnice, protože šroub nemá kam pokračovat, proto bych navrhoval, aby ty díry seděli na těch dírách s bočnicemi, ale byli použity jen některé. Co @kaklik  na to?

kittlerm, 2021-05-19:
Ano, už to mám odzkoušené a připravené, včetně možnosti nechat matku více "zapustit". Ale montáž není moc příjemná, chtělo by to přepracovat tu úchytku nohy

kittlerm, 2021-05-20:
Podobně jako je u ostatních dílů chybí zaslepení převisů nad šrouby ( např v https://github.com/ThunderFly-aerospace/Openscad_stdlib/commit/dabd1c7fbdc589b41f5c05d1f52508fff8bbd241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 )

kittlerm, 2021-05-20:
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

Jo říkal jsem si, že by pomohlo rozšířit rozteč děr

kittlerm, 2021-05-27:
@roman-dvorak @kakl : můžete mi prosím ukázat, jak správně přichytit kolečko? Objímka, ložisko nebo prostě na hulváta šroub?

roman-dvorak, 2021-05-27:
No, vzhledem k tomu, že se to kolečko reálně moc neotáčí, tak nebyl problém ho připvňovat šrubem se samojistnou matkou. A podložku z obou stran kola. Zkoušeli jsme to používat s kluzným pouzdrem, ale nebylo to skoro o nic lepší.

kaklik, 2021-05-31:
@roman-dvorak  Mám za to, že @kittlerm  by měl i ve větvi 4s nahradit tvoje [řešení montáže podvozkové nohy](https://github.com/ThunderFly-aerospace/TF-G2/commit/6e39729c614d194ab27217785f6a86a9e54323e9) s [přidanou kostkou](https://github.com/ThunderFly-aerospace/TF-G2/blob/4s/CAD/stl/888_1003.stl),  [novým dílem pro uchycení nohou](https://github.com/ThunderFly-aerospace/TF-G2/blob/8c0f04c6c630bffd450ea20d603912936f5b1760/CAD/stl/888_2004.stl).
Souhlasíš s tím?
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
kaklik, 2021-07-20:
Tak k původnímu uchycení podvozku, které je popsané v úvodu issue mám několik nových poznatků.  Aktuální realizace vypadá takto:

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

Potíž této konstrukce je, že bočnice na kterých drží podvozkové nohy se při zatížení rozjíždí do stran.  @slimonslimon  i @roman-dvorak  tuto záležitost řeší tak, že obě redukce na kterých podvozkové nohy drží propojili závitovou tyčí.

Podle mě by však bylo lepším řešením  do přední části navrhnout nový díl, který zastane funkci závitové tyče (podrží vzdálenost mezi montážními díly). Další funkce by byla jako aerodynamický kryt a také ochranný kryt konektoru akumulátoru a akumulátoru před nárazem.

kaklik, 2021-07-28:
Zde je ještě fotka aktuálně používané montáže.

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

kaklik, 2021-08-02:
Tak tady je ještě doplnění, jak současný způsob uchycení vypadá po havárii

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

Při dopadu navíc došlo k vytržení vodičů z napájecího konektoru na straně akumulátoru (na fotografii chybí). Tato situace ale zkomplikovala dohledávání, neboť vírník tak byl po havárii bez vysílače telemetrie.

kittlerm, 2021-08-04:
Co třeba takhle?
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

Přichytávalo by se to těmi spodními šrouby do nohou.

roman-dvorak, 2021-08-04:
Připadá mi (pouze z obrázku), že to zablokovalo přístup k napajecimu konektoru. A nevím, jestli to nekoliduje s bateriovým pouzdrem na nějaké větší baterky.

kaklik, 2021-08-04:
Jo, tvarově je to správně. :)

S tím přichytáváním na spodní šrouby od nohou..  Nevim moc jak to myslíš, ale to jsou zrovna šrouby, který se šroubují pěkně blbě, protože se k nim přes tu nohu moc nemůže.
Tenhle díl by to naopak chtělo mít možnost sundavat nějak relativně snadno.

Jako nejlepší řešení by mi přišlo, kdyby to šlo na vírník zepředu nasunout po zapojení konektoru. Bez použití šroubováku.
Myslím že by to šlo udělat tak, že to buď bude mít vhodný tvar s drážkami (které by tak asi musely být i na dílu pro uchycení nohou).  A nebo to tam můžem dočasně přichytávat lepicí páskou (to ale bude mít nevýhodu, že ten díl nenahradí funkci té závitové tyče, která to nyní stahuje.)

kittlerm, 2021-08-04:
> Připadá mi (pouze z obrázku), že to zablokovalo přístup k napajecimu konektoru. A nevím, jestli to nekoliduje s bateriovým pouzdrem na nějaké větší baterky.

Jo to se musí ošetřit, nevím jestli tam dávat parametr výšky z foto dílu na baterky, aby to lícovalo.

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

Ok, zkusím se nad tím zamyslet.

kaklik, 2021-08-30:
> Tohle by mělo sedět s baterkou a zasouvat se na spodek 2004 (tj. pomocného držáku s podvozkem), ještě udělám nějakou nacvakávací zarážku:
> 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

Tohle vypadá dobře!  Myslím že je to celkem řešení problému. Ještě jen musíme asi rozmyslet, jak to tam bude držet.   Paralelní s tím totiž vzniká [tenhle ušitý kryt](https://github.com/ThunderFly-aerospace/TF-G2/issues/39#issuecomment-908228346).  V případě jeho použití by bylo uchycení krycího dílu snadné. Protože na místě by pak držel po zapnutí zipu na textilním krytu.
Nepříjemné ale je, že pravděpodobně budeme vírník chtít používat i bez takového krytu.

kittlerm, 2021-09-02:
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
Je tam ještě nějaká změna vůči původnímu profilu na větvi mini, takže to musím upravit a otestovat variantu bez kupovaných nohou, tam je úplně jiná rozteč šroubů.

kaklik, 2021-09-18:
Při posledním testu se ukázalo, že je nepříjemně komplikované vymontovat díl motoru. Protože vyšroubování šroubů, které drží díl motoru brání roh podvozkových nohou

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
.

kittlerm, 2021-10-06:
Musím to ještě upravit, je tam malá vůle na lehký posun a hlavně při použití té varianty bez koupeného podvozku je tam málo materiálu, takže to má tendenci vyskočit. Zkusím zapracovat druhou pojížděcí lištu na druhé straně.

kittlerm, 2022-09-22:
Malinko jsem oříznul rohy - řešení je +/- pišvorc, asi by bylo lepší vytáhnout pozice šroubů z bočnice, ale prozatím takhle:
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

kaklik, 2022-09-22:
> Malinko jsem oříznul rohy - řešení je +/- pišvorc, asi by bylo lepší vytáhnout pozice šroubů z bočnice, ale prozatím takhle: 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

Mě tohle přijde úplně dobrý! :)  Jen to dej všechno do repozitáře tak, aby to příště šlo vytisknout celý a už to nech být. Víc času tomu není třeba věnovat.

kittlerm, 2022-09-22:
Dávno už to tam je, větev issue_86. Pro tisk jsem si vytáhl amf z artifaktů a oříznul v PrusaSliceru, abych to nemusel tisknout celé, ale jinak je to stejné jako z repositáře. Možná jen to dolní oříznutí není potřeba, to by šlo lehce změnit. Nebo udělat nový díl a mergnout 2002 a 2004? Co na to @roman-dvorak ?

slimonslimon, 2022-09-22:
2002 a 2004 bych nemegoval - zvětšilo by to samotnou nohu, a ta se musí dost často měnit. díky tomu přechodovému díu je ta výměna poměrně rychla.

já myslím, že ty úpravy můžeš rovnou namergovat do 4s

kaklik, 2022-09-23:
ok, považuji za vyřešené.

Closed 2022-09-23.

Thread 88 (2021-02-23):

Otestovat použití TFRPM a TFSLOT na jedné sběrnici.

roman-dvorak, 2021-02-23:
A jak to teď vlastně je s použitím TFRPM driveru na stejné sběrnici jako TFSLOT?  Funguje to, nebo ne?

Protože k TFSLOT se stejně I2C na pylon bude tahat, takže nevidím moc rozdíl v tom tam vést dvakrát I2C, nebo I2C a servokablík.

Z hlediska HW by bylo nejlepší řešení jen jedno I2C na které by byly připojeny oba senzory, díky tomu, že TFRPM je průchozí.  Vím ale že dříve jsme s tímto řešením měli potíže. Je tak otázka zda je to však relevantní i pro současný software?

_Originally posted by @kaklik in https://github.com/ThunderFly-aerospace/TF-G2/issues/76#issuecomment-780865480_

roman-dvorak, 2021-02-23:
Tady asi chybí nějaké "měření/pokusy" který by zjisti, kde je problém.

Driver neprovádí novou inicializaci RPM senzoru. Ale je potřeba vyzkoušet že reset rpm driveru stačí na obnovení funkčnosti.

_Originally posted by @slimonslimon  in https://github.com/ThunderFly-aerospace/TF-G2/issues/76#issuecomment-781265065_

kaklik, 2021-02-23:
Zatím jsem nerozběhl obě čidla, protože je potřeba změnit firmware, nicméně jsem měřil jak vypadá komunikace po I2C s TFRPM a objevil jsem tam tohle:

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

Je nepříjemné, že tam jsou ty krátké zákmity podstatně kratší než běžné bity. Může to způsobovat přeslechy a tím pádem hazardní stavy na sběrnici.

kaklik, 2021-02-24:
Tak jsem asi zprovoznil oba drivery. Nicméně zatím nemůžu potvrdit, zda to funguje, nebo nikoliv. Podezřelé ale je, že TFRPM senzor je nyní schopen dávat nesmyslné hodnoty.

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

kaklik, 2021-02-25:
Tak pokud se zapojí TFSLOT do série s TFRPM tak se s docela velkou pravděpodobností na SDA stane tohle:

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

Vznikne to následující sekvencí příkazů:

    icm20948i2c start -X -b 4

V tomto okamžiku je sběrnice ještě v pořádku. Rozbije se až následujícím příkazem:

    sdp3x_airspeed start  -X

Pokud se TFASPDIMU odpojí a připojí zpátky, tak se sběrnice zotaví a jsou na ní normální data.

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

kaklik, 2021-03-09:
Po vložení sériového rezistoru 82 Ohm mezi konektor a napěťový translátor na signál SDA se situace stabilizovala a zařízení začalo být použitelné.  Dalšího zlepšení lze zřejmě dosáhnout optimalizací hodnoty rezistoru. Viz issue: https://github.com/ThunderFly-aerospace/TFASPDIMU01/issues/5

Závěr však je, že obě zařízení na stejné sběrnici technicky mohou být provozovány.

Closed 2021-03-09.

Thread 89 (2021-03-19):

Úprava dat pro tisk na Průša mini

kaklik, 2021-03-19:
[Jednotlivé tiskové konfigurace](https://github.com/ThunderFly-aerospace/TF-G2/tree/mini/CAD/slicing) bude potřeba upravit, tak aby výsledné g-kódy byly spustitelné na tiskárně Průša mini.

Jsou dvě cesty, jak to udělat:

- Buď přepsat konfiguraci v každém jednotlivém tiskovém souboru, což je asi z počátku velmi snadné, ale bude vždy stejně náročné při každé změně
- Nebo udělat společnou konfiguraci a tu pak slučovat s konfiguracemi pro jednotlivé modely, [pomocí skriptu](https://github.com/ThunderFly-aerospace/processor3D/blob/master/src/merge_slic3r_conf.sh).

Ten výše uvedený slučovací skript, je výstupem od @JanKott a myslíme si, že je už velmi hotový, ale zatím nebyl prakticky použit.

kittlerm, 2021-03-19:
Zatím jsem udělal úpravu všech. Změny pro Mini jsem dal do mimi.ini - issue uzavřu až to zkusím vytisknout.

kittlerm, 2021-03-21:
První vlašťovka:
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

kittlerm, 2021-03-23:
Nosná podložka připravená k lepení:
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

kaklik, 2021-03-23:
> Nosná podložka připravená k lepení:

Super! :)   Je tam ale dost díra.. ;)

kittlerm, 2021-03-24:
> > Nosná podložka připravená k lepení:
>
> Super! :) Je tam ale dost mezera.. ;)

mno taky jsem si říkal. Obecně mi přijde, že ta tiskárna jede děsně rychle. Rozhodně rychleji, než při zpracování gcodu z PrusaSliceru. Je to taky možná tím, že se tam dává trochu víc extruderu na spodní a vrchní vrstvě, myslím, mám to zkusit poladit nebo to prostě obrousím (postprocessing) ?

kaklik, 2021-03-24:
>
> mno taky jsem si říkal. Obecně mi přijde, že ta tiskárna jede děsně rychle. Rozhodně rychleji, než při zpracování gcodu z PrusaSliceru. Je to taky možná tím, že se tam dává trochu víc extruderu na spodní a vrchní vrstvě, myslím, mám to zkusit poladit nebo to prostě obrousím (postprocessing) ?

Pokud ta tiskárna jezdí výrazně odlišně oproti průšasliceru, tak je to potřeba poladit. Protože to podle mě povede k tomu, že bude tisknout nepřesně.  Určitě je tam nějaké nastavení rychlostí, které teď asi nebude optimální.

Diskusi ohledně tisku těchto spojovaných dílů bych navrhoval přesunout [sem](#90). Každopádně si ale myslím, že když to obrousíš a slepíš, tak ti pak nebudou pasovat rozteče těch otvorů pro šrouby po celé délce.

kittlerm, 2021-03-24:
Ok, zkusím se na ty parametry podívat.

kittlerm, 2021-03-24:
Udělal jsem úpravy rychlostí podle PrusaSliceru (PrusaSlicer 0.20mm QUALITY @ MINI, Original Prusa MINI & MINI+)

kittlerm, 2021-03-24:
Ještě je otázka, zda nepřevzít i ostatní parametry ze záložky Printer?

kittlerm, 2021-03-25:
Provedl jsem upravy rychlosti, je to lepsi, ale neni to stejne, PrusaSlicer dela pomaleji externi perimeter:
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

roman-dvorak, 2021-03-25:
To je asi potřeba vyexportovat konfigurační ini od Prusi a porovnat celou konfiguraci ini diffem od @JanKott.

Protože to nastavení se nebude lišit pouze v parametrech ze záložky printer (rozdělení parametrů v některých částech není úplně nejlogičtější)

kittlerm, 2021-03-25:
> To je asi potřeba vyexportovat konfigurační ini od Prusi a porovnat celou konfiguraci ini diffem od @JanKott.

Diff umím udělat, ale já mam spíš problém, že nevím, co mam převzít? Protože jak jsem vyrozuměl: @kaklik nechce, aby se to Prušou slicovalo. Já dokonce nemám ani problém změnit slicer, už jsem to zkoušel a mělo by to jít.

> Protože to nastavení se nebude lišit pouze v parametrech ze záložky printer (rozdělení parametrů v některých částech není úplně nejlogičtější)

Souhlas, ale ten hlavní problém je, že neexistuje něco jako jako essential.ini, kde by těch nastavení nebylo stovky, ale jen ty opravu důležité změny.

roman-dvorak, 2021-03-25:
Ano, Průšův slicer nechceme používat, protože nelze použít v rámci actions (a jiné automatizace generování kódu)

Průšův Slicer vychází ze Slic3r. A díky tomu by (snad) stále velká většína parametrů měla být kompatibilních.

Možná by bylo dobré, kdybys mohl takové porovnání nějak připravil třeba do google tabulky abychom se nad tím mohli společně pobavit. Co by mohlo být důležité použít z jejich konfiguarace a co naopak. Případně jak takový essetnial.ini vyrobit. Protože takového stavu chceme dosáhnout. Abychom pro konkrétní tiskárny/modely upravovali jen dílčí konfigurace.

kittlerm, 2021-03-25:
> Ano, Průšův slicer nechceme používat, protože nelze použít v rámci actions (a jiné automatizace generování kódu)
To si myslím, že je chiméra, zkoušel jsem to lokálně, nevidím důvod, proč by to nešlo v actions na githubu.

> Průšův Slicer vychází ze Slic3r. A díky tomu by (snad) stále velká většína parametrů měla být kompatibilních.
> ...
ano, zde je tabulka: https://docs.google.com/spreadsheets/d/1DVKDlwXKmDDPxDcK8vhCZcuokp0WVd9-VvMJ01STOAw/edit?usp=sharing

roman-dvorak, 2021-03-25:
> To si myslím, že je chiméra, zkoušel jsem to lokálně, nevidím důvod, proč by to nešlo v actions na githubu.

Dlouho jsem ho neviděl (to bych asi měl někdy napravit). Ale když jsem to zkoušel naposled, tak tam byl nějaký problém, že mu nešlo dát konfiguraci jakou má používat.

Tabulka je super.

kaklik, 2021-03-25:
> > To si myslím, že je chiméra, zkoušel jsem to lokálně, nevidím důvod, proč by to nešlo v actions na githubu.
>

Hlavní problém o kterém vím, je že díky tomu že průša slicer je oddělený od Slic3ru. Tak nám nedovede poskytnout důležité hodnoty - posuny modelů při slicování a i jejich těžiště.

kittlerm, 2021-03-26:
> posuny modelů při slicování

to jako myslíš při "arrange"? Můžeš mu ale vynutit pozici z cmd příkazu.

> a i jejich těžiště

na to je nějaký externí program ne? Nebo slic3r to píše rovnou do gcodu? (to jsem si nevšiml). Každopádně jde forknout ne?

Každopádně vytištěné gcody na MINI jsou podle mého laického přístupu dobré. Odtržení od podložky použitím prusasliceru podle mě nevyřeší. Stávalo se mi to i toho letadélka edge aj. částí, když mají malou plochu na desce.

kaklik, 2021-03-29:
@roman-dvorak  Ještě při řešení tisku modelu 888_1002  @kittlerm  přišel s návrhem, že by se v printplate modelu zapínal tisk brimu tímhel způsobem:

    //@set_slicing_config(../../slicing/default.ini)
    //@set_slicing_config(../../slicing/brim.ini)

Kde brim.ini by obsahoval pouze změněné konfigurační hodnoty proti default.ini, které by zapínaly brim.  Processor3D by tak měl oba soubory sloučit, s tím že vyhrávají parametry z posledního.
Já to chápu jako nový návrh způsobu jak zadávat slučování konfigurací pro tisk.  Je pak otázka, jakými dalšími způsoby se pak slučovací skript má volat?

roman-dvorak, 2021-03-29:
V návrhu processoru3d se uvažovalo o tom, že by se parametry jako brim zapínaly přímo z openscadu. Tedy že by nemusel existovat ini jen kvůli Brimu.

kittlerm, 2021-03-29:
Přijde mi, že počítat to v openscadu je zbytečné harakiri, nehledě na to, že by to mohlo posunout těžiště, ne? (mno asi to nebude tak významná položka)

kaklik, 2021-03-29:
> Přijde mi, že počítat to v openscadu je zbytečné harakiri, nehledě na to, že by to mohlo posunout těžiště, ne? (mno asi to nebude tak významná položka)

Domnívám se, že @roman-dvorak  asi nemyslí modelovat brim v openscadu, ale myslí do parametrů sliceru jen přímo přidat zapnutí brimu...  Ale popravdě nevím, jakým způsobem je to v návrhu processor3Duvažováno.

JanKott, 2021-03-30:
Přímo do OpenScadu se dá vložit i parametr, například takto:
`//@set_slicing_parameter(infill_only_where_needed, 0)`

kittlerm, 2021-03-30:
A bude tam teda více řádků?
```
//@set_slicing_config(../../slicing/default.ini)
//@set_slicing_config(infill_only_where_needed, 0)
```

JanKott, 2021-03-30:
Ano, ale konfigurace jen jedna. Takto:
```
//@set_slicing_config(../../slicing/default.ini)
//@set_slicing_parameter(infill_only_where_needed, 0)
//@set_slicing_parameter(fill_density, 1%)
```

kittlerm, 2021-03-31:
Bohužel to ale nefunguje, nastavení jsem snad udělal správně:
https://github.com/ThunderFly-aerospace/TF-G2/blob/mini/CAD/src/printplate/printplate_888_1002.scad
neodpovídá nastavení v gcodu:
https://raw.githubusercontent.com/ThunderFly-aerospace/gcodes/TF-G2/refs/heads/mini/edee/gcode/TF-G2_printplate_888_1002.gcode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

```
; brim_width = 0
```

kittlerm, 2021-03-31:
Možná by stálo za to, kdyby processor3D udělal do artefaktů to nastavení s popisky, co (jaký soubor) to nastavení změnil.

roman-dvorak, 2021-05-21:
> Možná by stálo za to, kdyby processor3D udělal do artefaktů to nastavení s popisky, co (jaký soubor) to nastavení změnil.

asi nechápu, co to má obsahovat?

kittlerm, 2021-05-21:
> asi nechápu, co to má obsahovat?

Komentáře, ze kterého souboru pochází ta hodnota.

kaklik, 2021-06-26:
> Provedl jsem upravy rychlosti, je to lepsi, ale neni to stejne, PrusaSlicer dela pomaleji externi perimeter:
> 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

Tento díl jde nyní na Průša mini+ bez problémů tisknout. Funguje tisk i mnoha dalších dílů.  Tudíž bych řekl, že toto issue je již vyřešeno. :)

Closed 2021-06-26.

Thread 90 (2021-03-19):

Řešení způsobu tisku dlouhých dílů

kaklik, 2021-03-19:
TF-G2 nyní obsahuje dva typy dílů, které nejdou vytisknout na běžné tiskárně.

- [Spodní podložka trupu 888_1001](https://github.com/ThunderFly-aerospace/TF-G2/blob/4s/CAD/stl/888_1001.stl)
- [Bočnice trupu](https://github.com/ThunderFly-aerospace/TF-G2/blob/4s/CAD/stl/888_1003.stl)

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

Vyřešení tohoto problému dost souvisí s issue #89 Neboť by zřejmě bylo nejlepší, aby díly byly děleny tak, aby se vešly na danou tiskárnu.

kittlerm, 2021-03-24:
Rozdělené díly na PrusaMini mají přehyb na svrchní straně, takže lepení může být trochu problematické:
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

Prozatím to zkusím zbrousit (jen ten přesah), @kaklik se obává, že dojde k nepřesnosti na rozteči děr, já si myslím, že se pohybujeme v rozumném přesahu (do milimetru), takže to nebude vadit. Úpravu pomocí parametrů tisku budu řešit v #89

kaklik, 2021-03-24:
Zkoušel jsem se zamyslet nad postupem jak dělit 3D tištěné modely, tak aby šly lepit nebo i sešroubovat. Nějak jsem nevymyslel nic chytřejšího než tohle:

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

[Přikládám zdrojový soubor nákresu](https://github.com/ThunderFly-aerospace/TF-G2/files/6196600/3D_printed_parts_connection.zip)

Nevím zda matematicky vůbec lze vymyslet více řešení. Neboť potíže s tím jsou tyhle:

1. tiskárna má kulatou trysku, což znamená že na všem vytiskne radius.
2. Plocha dílů musí být co největší, aby co nejméně záleželo na kvalitě spojení (nanesení lepidla, kvalita svaření a podobně)

Potíž nastává v tom, že čím více se vytvoří radiusů na jedné straně, tím ostřejší tvary vznikají na druhé. Z toho mi vychází, že tato záležitost má možná i geometricky velmi limitovaný počet řešení.

Jako nejrozumnější mi ale připadá díl dělit v openscadu, takovým způsobem, že by v modelu byly body, kde může vést spline a podle tohoto spline pak model rozdělit. Konkrétně na modelu bočnice by to pak zřejmě vypadalo nějak takhle:

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

kittlerm, 2021-03-24:
Po jemným obroušení (papírem 1000) vypadá spoj dobře:
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

Každopádně pevnostně to bude slabé, předpokládám, že se tam ale vystřídá ukotvení bočnice, takže by to nemusela být taková tragedie?

kaklik, 2021-03-25:
> Nějaký test pevnosti? Nebo u podložky je to zbytečné?

U TF-G2 jedinné díly, které potřebují pevnostní test před letem jsou rotorové listy. Ale ty stejně asi vyrábět nebudeš.  U ostatních dílů se pozná až po přistání/dopadu, jak na tom pevnostně jsou. :)

kittlerm, 2021-04-07:
@kaklik našel způsob jak u Průshy vytvářejí puzzle pomocí modifikátorů: https://blog.prusaprinters.org/print-your-own-3d-puzzles_29817/

kaklik, 2021-05-18:
Další možnost je na dělené díly přidat "domečky" které se vzájemně sešroubují šrouby. Výhoda takového řešení by byla v tom, že by nebylo nutné měnit třeba celou bočnici, ale jen nějaký segment.
Taková změna by mohla zjednodušit i servis vírníku. Neboť v momentálním stavu vyměnit bočnici vírniku, znamená vírnik úplně rozebrat a složit.
Je možné, že šrouby by šly kombinovat s tvarovými zámky pro rozvedení sil do větších ploch, což by znamenalo, že na bočnicích by pak nebyly žádné lepené spoje.

kaklik, 2022-01-28:
Ta výhoda dělení bočnic rozebíratelnými spoji, se celkem potvrzuje na posledních nehodách, kdy je zbytečně nutné měnit celé bočnice a podložku když je poškozena jen její část.

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

Společně s vyřešením tohoto problému by zřejmě chtělo přejít v málo rozebíraných spojích na použití samořezných šroubů do plastu.
Velmi by to zrychlilo výrobu nových kusů vírníků a odlehčilo konstrukci.

kaklik, 2022-08-25:
K tomuto issue už existuje implementace dělené bočnice:

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

Zatím to předpokládá lepení lepidlem, což neumožňuje selektivní výměnu. Na spodní části je proto jiné experimintální dělení, které ale zas spotřebovává poměrně hodně materiálu.

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

roman-dvorak, 2022-08-25:
> Zatím to předpokládá lepení lepidlem, což neumožňuje selektivní výměnu.

Tohle řešení defaultně nepředpokládá lepení lepidlem. Cílem tohoto slepení bylo porovnat chování slepené a neslepené bočnice. A mým závěrem je, že to vůbec není potřeba lepit a myslím, že to může být provozováno tak, jak je to na druhé straně tohoto složeného trupu.

Puzzle zámek v podložce potřebuje zvětšit tolerance (protože je to těžko rozebratelné) a zřejmě ani není nutný "schod" pro zvětšení styčné plochy.

kaklik, 2023-06-02:
Zjistil jsem že tahle technika se jmenuje [Dovetail joint](https://en.wikipedia.org/wiki/Dovetail_joint) a jsou tak dohledatelné další detaily a některé triky jak to udělat dobře.

kaklik, 2023-08-15:
Myslím, že mě napadl vůbec nejlepší způsob, jak vyřešit to napojování na relativně tenkých dílech, kde není moc materiálu na puzlle a podobné zámky.

Abych tu nemusel kreslit náčrt, tak si k vysvětlení půjčím tenhle obrázek:

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

Podstatné jsou zde zejména spoje e) a i). Tyto dva spoje lze v našem případě zkombinovat bez použití lepidla.  Řešení by pak vypadalo tak, že spojovací díl by byl zapuštěn v úrovni dvou spojovaných dílů. V případě bočnic by to znamenalo, že v místě spoje bočnice vznikne ještě další díl, který v podstatě vznikne oddělením několika tiskových vrstev ze základního materiálu. (Kvůli tomu, aby to bylo možné vytisknout, tak zřejmě z vnější strany bočnic, která je při tisku směrem k trysce)

Při spojování bočnic by se pak všechny díly daly přes sebe a prošroubovaly šrouby. Výhody jsou:

- Nepotřebuje to lepidlo.
- Nepřidává to žádný materiál navíc (kromě možná několika šroubů)
- Nevzniká zde žádný "tektonický zlom", kde se soustředí vzájemný pohyb a síly z dílů bočnic při jejich namáhání.
- K výměně stačí jen vytisknout nové díly a znovu je našroubovat na stejné místo.

Nevýhoda možná je to, že při poškození je dost pravděpodobné, že to zasáhne hned dva díly najednou.  To by ale asi nemělo být tak kritické pokud se vhodně uspořádají tiskové sestavy.

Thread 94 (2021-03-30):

Odlehčení podložky - spodní díl trupu

kaklik, 2021-03-30:
[Podložka trupu](https://github.com/ThunderFly-aerospace/TF-G2/blob/mini/CAD/stl/888_1001.stl) nyní patří mezi nejhmotnější díly vírníku TF-G2. Důvodem je patrně předchozí snaha realizovat konstrukci tak, aby umožnila vyřezávání z plochého materiálu, například z překližky. Pokud se ale tento koncept zruší a lépe se využijí možnosti 3D tisku, tak výsledný tvar může být výrazně komplikovanější a tím efektivněji využívat materiál.

Podložku by mohly zlepšit následující úpravy:

- [ ] Odlehčení podložky v podobném stylu jako jsou bočnice - taková změna by pravděpodobně vyžadovala montáž podložky "vzhůru nohama" oproti současnému stavu. Tato změna by ale zřejmě zjednodušila skládání vírníku.
- [ ] Matice by se hodilo do podložky více zapustit, aby nemohlo dojít k jejich protočení při montáži
- [ ] Průřez materiálu v okolí montážních otvorů by měl být zachován, aby byl umožněn rozklad sil do větších ploch viz. issue #92
- [ ] Na podložce by se hodilo více montážních děr v ploché části. S  tím že některé by měly umožňovat zapuštění matic. viz například montáž držáku ocasní trubky. #92
- [ ] Podložka obsahuje ortogonální odlehčovací otvory, které z hlediska využití materiálu nejsou příliš efektivní. výhodnější je příhradová konstrukce využitá například na bočnicích, nebo u podvozkových nohou.

kaklik, 2021-05-17:
@roman-dvorak  vytvořil kroužky v okolí existujících otvorů pro šrouby, což by mělo řešit problém se zachováním průřezu materiálu:

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

Jeden z bodů je tak vyřešen.

kaklik, 2021-06-04:
Díky [budoucí úpravě TFGPS](https://github.com/ThunderFly-aerospace/TFGPS01/issues/29), začne být toto issue důležité. Neboť je nutné umístit autopilota v TF-G2 tak, aby byl přístupný servisní USB-C konektor na něm.

kaklik, 2021-09-19:
Podložku bude potřeba odlehčovat společně s řešením #90 Neboť na podložce je nyní tento díl.

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

Který se používá pro připevnění úchytů ocasní trubky a autopilota. Tento díl by však chtělo upravit tak, aby byl zapuštěn do odlehčené podložky.
Předpokládám však, že při řešení tisknutelnosti dlouhých dílů bude použita nějaká obdobná technika vystužení a následného spojování.

kaklik, 2022-08-25:
@roman-dvorak  implementoval do podložky změnu šroubů za šrouby do plastu. V návrhu jsou ale zřejmě nesprávné tolerance, protože při utažení šroubů dochází ke zbělání plastu v místě závitu.

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

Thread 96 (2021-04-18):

Odlehčení šroubů pro vaničku akumulátoru

kaklik, 2021-04-18:
Pro uchycení vaničky s akumulátorem se nyní používají [šrouby s rýhovanou hlavou](https://eshop.killich.cz/eshop/spojovaci-material/srouby-zatky/srouby-metricke-ostatni/din-464-sroub-ryhovana-hlava/).

Tyto šrouby fungují velmi dobře, ale mají dvě nevýhody:

1. Jsou poměrně hmotné, neboť obsahují hodně materiálu
2. Nejsou dobře dostupné, protože jde o speciální typ šroubu

Řešením by mohlo být použít naopak běžně dostupný [šroub se šestihrannou hlavou](https://eshop.killich.cz/eshop/spojovaci-material/srouby-zatky/srouby-s-sestihrannou-hlavou/din-933-sroub-sestihranny-celozavit/).  K tomuto šroubu by pak bylo potřeba navrhnout klobouček s rýhami, který bude sloužit k utahování.
Takový návrh může vycházet ze současného [dílu pro dotahování matice rotoru](https://github.com/ThunderFly-aerospace/TF-G2/blob/4s/CAD/stl/888_4007.stl).  Z něj stačí pouze odstranit otvor pro provázek a celý díl zkrátit.  Možná bude potřebné přidat osazení na straně šroubu, které zmenší průměr válce okolo hlavy šroubu, tak aby mohl být šroub utažen i mezi žebra na bočnicích.

Tady je ukázka principu na původním dílu rotorové matice:

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

kaklik, 2021-05-17:
@llucka Ahoj,  je prosím zde nějaká změna?  @kittlerm  by se myslím totiž tahle úprava celkem hodila, aby při výměně akumulátorů nemusel používat imbus. A nebo shánět speciální šrouby.

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

llucka, 2021-05-18:
hotovo - je připravený printplate pro 4 díly

kaklik, 2021-05-18:
> hotovo - je připravený printplate pro 4 díly

@llucka  Super! :)

@kittlerm  máš nějaké šrouby M3 se šestihrannou hlavou, aby jsi to mohl rovnou vyzkoušet? Nebo budeš potřebovat nějaké dodat? Asi by se mi hodilo znát alespoň nějaký odhad délky, která by tam mohla pasovat, což se dá vyzkoušet se šroubem s válcovou hlavou.

kittlerm, 2021-05-18:
M3 se šestihrannou hlavou nemám (teda ne ze skladu) nevím jestli mam hledat nějaký v mém pracovním bordelu, ale obávám se, že tam budu mít jen M4, protože hlava určitě bude mít rozměr nějaké půlky jako 5.5 a taký jsem si jist, že jsem do těď nepotkal ;)

kaklik, 2021-05-19:
> M3 se šestihrannou hlavou nemám (teda ne ze skladu) nevím jestli mam hledat nějaký v mém pracovním bordelu, ale obávám se, že tam budu mít jen M4, protože hlava určitě bude mít rozměr nějaké půlky jako 5.5 a taký jsem si jist, že jsem do teď nepotkal ;)

Dobrá, šrouby seženu, ale potřeboval bych nějaký odhad jak dlouhé.  Myslíš že bys prosím mohl ten nový díl vytisknout a zkusit třeba pomocí těch šroubů s válcovou hlavou odhadnout potřebnou délku šroubu, případně nějaké jiné geometrické úpravy modelu?

V repozitáři to vypadá teď takhle:
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

kaklik, 2021-05-19:
Počká to.

Ještě mezitím bych navrhoval ten printplate_battery_screw.scad přejmenovat na printplate_888_6002.scad, s tím že by asi bylo hezký, kdyby se pouzdro na baterky mohlo jmenovat printplate_888_6001.scad  místo současného printplate_888_1018.scad. Ale nevim, jestli to nevyrobí moc konfliktů při přejmenování ve všech větvích.

Ten samotný díl vevnitř `hlava_na_sroub()` by asi bylo fajn, kdyby se mohl jmenovat v angličtině.   Takovému typu šroubu se říká  [knurled thumb screw](https://eshop.i-fasteners.com/e-shop/m3x8-zinc-5-8-knurled-thumb-screws-thin-type-din-653_11622503008.html), takže bych to pojmenoval nějak jako `knurled_thumb()` třeba.

kittlerm, 2021-05-20:
Trochu jsem si to upravil na válcovou hlavu, aniž bych změnil délkové rozměr šroubu a M3x12 nechytne matku. M3x14 v pohodě:
https://photos.app.goo.gl/6fBfQecp4DZAsD1g6

Pokud bychom stáhli výšku vroubkaté objímky o 1mm, pořád by se dala pohodlně používat a bylo by možné použít M3x12. (ověřil jsem to) ale to chycení je malé, chtělo by to tak 1.5mm odebrat:
https://photos.app.goo.gl/ngZ7d45pKtFCFwMp7

kaklik, 2021-05-21:
> Trochu jsem si to upravil (lokálně u sebe) na válcovou hlavu, aniž bych změnil délkový rozměr šroubu a M3x12 nechytne matku.

Tu úpravu na válcovou hlavu jsi si dělal zbytečně.. Ona válcová hlava jde dát do šestihranné díry pro matici.. ;)

> Pokud bychom stáhli výšku vroubkaté objímky o 1mm, pořád by se dala pohodlně používat a bylo by možné použít M3x12. (ověřil jsem to) ale to chycení je malé, chtělo by to tak 1.5mm odebrat:
>

Z těch fotografií mi přijde, že aktuální objímka zbytečně sežere velkou část délky šroubu.  Navrhoval bych proto šroub více zapustit do vroubkované objímky, aby nebyla taková délka spotřebovaná objímkou.  Aktuální výška objímky vyhovuje dobře, aby se dala pohodlně chytit na členité bočnici a otáčet?
Pokud ano, tak by zapuštění šroubu myslím šlo pohodlně zvětšit minimálně o 2mm (aktuálně vidím, že je hlava šroubu téměř zarovnaná z koncem objímky).

kittlerm, 2021-05-21:
> Ona válcová hlava jde dát do šestihranné díry pro matici.. ;)

mno alespoň nebylo zbytečné vstávat... :D

> Aktuální výška objímky vyhovuje dobře, aby se dala pohodlně chytit na členité bočnici a otáčet?

Ano:
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

I zkrácená varianta jde ale dobře a ještě kousek by šel ubrat:
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

kittlerm, 2021-05-21:
> (aktuálně vidím, že je hlava šroubu téměř zarovnaná z koncem objímky)

Valcova hlava je trochu vyšší, ale to zapuštění jsem neměnil schválně, abych měl stejnou hodnotu délky šroubu i s šestihranem.

roman-dvorak, 2021-05-29:
Z této debaty netuším, jaký je závěr?
Bylo by dobré sem napsat konkrétní požadavky na úpravy. O kolik co zkrátit; popř. zapustit.

kaklik, 2021-05-30:
> Z této debaty netuším, jaký je závěr?
> Bylo by dobré sem napsat konkrétní požadavky na úpravy. O kolik co zkrátit; popř. zapustit.

Já si ten model ještě nevytiskl..  Ale @kittlerm  jsem předal různé délky šroubů M3 se šestihrannou hlavou a ten má už nějakou verzi vytištěnou. Takže očekávám, že @kittlerm  má teď nejlepší podmínky pro to definovat, co je špatně a co je potřeba změnit.

kittlerm, 2021-05-30:
Měla by se upravit na hloubka zapuštění, je tam velká část na šroubu, která je zbytečná. Každopádně zítra to přetisknu a vyzkouším.

kittlerm, 2021-05-31:
@roman-dvorak bohužel, kod [TF-G2_printplate_battery_screw.gcode](https://github.com/ThunderFly-aerospace/gcodes/blob/ThunderFly-aerospace/TF-G2%2F4s%2Fmini/gcode/TF-G2_printplate_battery_screw.gcode) není aktuální pro Mini.

kaklik, 2021-06-17:
> @roman-dvorak bohužel, kod [TF-G2_printplate_battery_screw.gcode](https://github.com/ThunderFly-aerospace/gcodes/blob/ThunderFly-aerospace/TF-G2%2F4s%2Fmini/gcode/TF-G2_printplate_battery_screw.gcode) není aktuální pro Mini.

Tak příčina byla v tom, že původní prinplate neobsahoval nastavení pro slicer. Nyní jsem díl [přejmenoval aby odpovídal ostatnímu  číselnému značení](https://github.com/ThunderFly-aerospace/TF-G2/blob/4s/CAD/src/printplate/printplate_888_1020.scad).  Zároveň jsem i přidal nastavení pro slicer. Takže když generování doběhne, tak si myslím, že to bude možné rovnou vytisknout a vyzkoušet.

Do knihovny jsem i přidal nějakou základní parametrizaci. Takže hlavní geometrické rozměry by mělo jít změnit [tady](https://github.com/ThunderFly-aerospace/TF-G2/blob/c4e445a07dbc138db634a895908c79127e00e91e/CAD/src/888_1020.scad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).

Až bude vybraná vhodná délka šestihranného šroubu, který tam pasuje a upraveny geometrické rozměry tak, aby to šlo pohodlně používat, tak se už může tohle issue uzavřít. :)

kittlerm, 2021-06-24:
Použití M3x12 je pohodlné, možná pro chycení krabicky baterie trochu zbytečně dlouhý, ale zase se lépe chytá začátek do matičky.
M3x10 také jde, ale musí se trochu víc přitlačit, než se chytne matky.
M3x14 nejde dotáhnout, narazí na stěnu.

Co se týče ovládání, tak je to už trochu na těsno k tomu boku, ale jde to používat.
Větší zapuštění asi není vhodné pro použití M3x10, protože se musí prstem zatlačit dovnitř, aby se to chytlo.

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
z leva M3x14,12,10

kaklik, 2021-06-26:
> Použití M3x12 je pohodlné, možná pro chycení krabicky baterie trochu zbytečně dlouhý, ale zase se lépe chytá začátek do matičky.

Co teda použít M3x12 a o kousek prodloužit tu válcovou část aby ovládací kolečko bylo trošku dál od trupu? :)

kittlerm, 2021-06-28:
Ok, upravím a vyzkouším.

kittlerm, 2021-07-01:
Mělo by to být hotovo ve větvi 4s.

kaklik, 2021-08-04:
Ok potvrzuji, šroub M3x12 je adekvátní náhradou dosud používaného šroubu s vroubkovanou hravou. :)

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

Closed 2021-08-04.

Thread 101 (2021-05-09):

Tail rudder servo cable extension

kaklik, 2021-05-09:
Současné konstrukční řešení předpokládá prodlužovací kabel protažený skrz trubku ocasu až k zadnímu servu.
Servokabel se spojuje s prodlužovákem vyvedeným z autopilota ve spodní části trupu.
Potíž tohoto řešení je v tom, že asi neexistuje komerčně dostupný prodlužovací servokabel, který by bez úprav bylo možné protáhnout ocasní trubkou.

Je tak několik možností, jak tuto situaci vyřešit:

- Vyrábět speciální prodlužovací kabely jen s hřebínkem a na konektor ocasního serva zajištěné bužírkou.
- Zkusit seříznout hrany od [prodlužováku s klipem]( https://www.peckamodel.cz/kabel-serva-prodluzovaci-spm-jr-s-klipem-hd-50cm) a klip použít k zajištění
- Použít ocasní trubku s průměrem, kam se vejde neupravený prodlužovací kabel včetně zajišťovacího zámku
- Úplně zrušit ocasní trubku a ocas překonstruovat tak, že bude navazovat na trup.

kaklik, 2021-07-06:
Vzhledem k aktuální situaci, kdy nemáme čas na výrobu speciálních prodlužovacích kabelů, které navíc mají minimální přínos ke kvalitě konstrukce. Bych navrhoval, aby ocas byl upevňen přes tlustší trubku s vnitřním průměrem asi 11mm. Takové řešení může zůstat do doby, než bude možné se zbavit ocasu na trubce úplně a nahradit ho ocasem upevněným za pylon a trup.

kaklik, 2021-08-14:
Kromě zvětšení průměru ocasní trubky a jejích úchytů, což jsem již provedl, by to zřejmě chtělo ještě zpevnit zadní část trupu, kam se ocasní trubka montuje.
Zamezilo by se tím i časté destrukci spodní části trupu během nezdařeného přistání.

Navrhoval bych to řešit tímto způsobem:

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

- Současné spony ocasní trubky by se tak montovaly šrouby ze vně podložky, což by výrazně usnadnilo jejich výměnu.
- Pod autopilotem by byla další tenká podložka s místem pro nalepení suchého zipu pro montáž autopilota. (Suchý zip by tak nebylo nutné dodatečně připevňovat tavným lepidlem)
- Do podložky pod autopilotem by byly vloženy matice a zafixovány přelepením suchým zipem, nebo lepící páskou, aby při výměně spon nemohly snadno vypadnout.

kaklik, 2021-08-21:
Vyřešeno plackou 888_1021.scad

Closed 2021-08-21.

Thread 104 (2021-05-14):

Collision of code-wheel cap and pylon parts

roman-dvorak, 2021-05-14:
V příapdě větší výchylky dochází ke kolizi mezi rolničkou rotoru a pevnou boční částí pylonu.

V dílu 888_1010 je potřeba zmenšit část nad šroubem tvořící osu rotoru. Zároveň by bočnice mohly být trošku tlustší, protože se zde přenáší celá hmotnost vírníku.

Provizorní oprava vypadala takto:
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

- [ ] Vyřešení kolize
- [ ] Tlustší boční stěny

kaklik, 2021-05-14:
Nevím přesně co, myslíš tím "zmenšit část nad šroubem tvořící osu rotoru".  Ale domnívám se, že zásadní příčina vzniku kolize spočívá v tom, že

1. Prodloužily se páky serv, což celkově zvětšilo rozsahy rotorové hlavy
2. Došlo k rozšíření dílu [888_1011](https://github.com/ThunderFly-aerospace/TF-G2/blob/4s/CAD/stl/888_1011.stl), který tak výrazně snížil rozsah v ose roll.

Díl [888_1011](https://github.com/ThunderFly-aerospace/TF-G2/blob/4s/CAD/stl/888_1011.stl) je mimochodem v repozitáři zjevně v jiné verzi, než která je na fotografii, což není moc dobře.

Každopádně primární směr ve vyřešení tohoto issue, vidím v navrácení dílu [888_1011](https://github.com/ThunderFly-aerospace/TF-G2/blob/4s/CAD/stl/888_1011.stl) do původní velikosti zúžením rozestupu mezi horními úchyty.  Další krok pak je sehnat a použít kratší páky u serv a nebo táhla u serv přešroubovat na díru pák nejblíž ose serva.

roman-dvorak, 2021-05-14:
V repozitáři je již novější verze.

kaklik, 2021-06-26:
@roman-dvorak  Není tohle už náhodou vyřešené a ověřené posledním testem? :)

Closed 2021-06-26.

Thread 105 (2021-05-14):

Change of actuators (servos) in rotor-head and in rudder

roman-dvorak, 2021-05-14:
Nově se budou používat serva [BMS-115HV](https://www.blue-bird-model.com/products_detail/55.htm). Primárním důvodm je, že je potřeba posunout servo na rotorové hlavě trochu dopředu a usnadnit montáž. To aktuálně nelze realizovat z důvodu, že by bylo nutné tisknout vodorovný převis. (nyní se to tiskne na podložku)

Stejné servo by se pak použilo do ocasu. Kde se to také zjednoduší. Připevňení serv by v obou případech bylo pomocí samořezných šroubků.

- [x] Úprava rotorové hlavy 4S
- [ ] Úprava ocasu
- [X] úprava pylonu pro master verzi.

roman-dvorak, 2021-05-18:
Ve větvi 4s je tato úprava už implementována. Jen otvor na samořezný šroub je zřejmě moc velký.

kaklik, 2021-05-18:
> Ve větvi 4s je tato úprava už implementována. Jen otvor na samořezný šroub je zřejmě moc velký.

A myslíš tím, že jsou implementovány všechny body zmíněné výše?  Protože ani jeden z nich nevidím zaškrtnutý, což je trochu matoucí.

roman-dvorak, 2021-05-18:
Ocas není implementovaný vůbec. A 4S rotorová hlava má zmíněný nedodělek.

kaklik, 2021-05-18:
> Ocas není implementovaný vůbec. A 4S rotorová hlava má zmíněný nedodělek.

Ok, a co znamená ten bod "úprava pylonu pro master verzi." ?

roman-dvorak, 2021-05-18:
asi to znamená se rozhodnout, která serva se pro master verzi budou používat. Pokud tyto s příčnou montáží (BMS-115HV) tak snížit ten sloupek pro přišroubování a změnit směr díry, kterou se šroubují za přírubu serva.

Tyto pylony už jsou nemergeovatelné.

roman-dvorak, 2021-05-29:
> Ve větvi 4s je tato úprava už implementována. Jen otvor na samořezný šroub je zřejmě moc velký.

Opraveno.

roman-dvorak, 2021-06-26:
Vypadá to, že u ocasních ploch bude provedeno více úprav. Aktuálně úprava ocasu pro připevnění serva nemá moc význam. Na pár dalších kusech lze řešit tavným lepidlem.

Umístění serva na rotorové hlavě bylo několika lety otestováno a vypadá jako dobré.

kaklik, 2021-06-26:
Já bych tu úpravu ocasu pro lepší montáž serva docela rád viděl implementovanou.. To tavné lepidlo se mi nezdá jako moc dobré řešení, měli bychom se totiž už blížit k nějakému velmi definovanému způsobu montáže.
Také bych rád, aby ocasní servo bylo lépe kryto při nárazu ocasu do země, aby to nebyl první díl o který se vírník zasekne.

Closed 2021-06-26.

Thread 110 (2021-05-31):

Try to use stlsort alternative from nopscad

roman-dvorak, 2021-05-31:
[Stlsort](https://github.com/hroncok/stlsort) umí v sortovaném STL záporné nuly. Viz issue: https://github.com/hroncok/stlsort/issues/1#issuecomment-851695164. Vytváří to "falešné" commity v gitu. Existuje alternativa z knihovny nopscad, která tohle má údajně ošetřené. Jsou dvě možnosti, jak to vyřešit:

 - Použít alternativní STLSORT z nopscadu;
 - nebo vytvořit parametr, který to v STLSORTu umí vypnout.

kaklik, 2021-05-31:
Hmm, tohle ale asi není issue TF-G2.. Patříto myslím spíš někam do workflow..

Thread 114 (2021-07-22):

ThunderMill - Generation of Kicad edge layer from OpenSCAD

roman-dvorak, 2021-07-22:
Aby bylo možné vyrobit desku, která bude vycházet z OpenSCAD návrhu, je potřeba dodržet následující postup. Je potřeba, abyste se @ChroustJan a @Alsa-Tucnak dohodli, kde kterou část udělá. Já bych navrhoval, aby @Alsa-Tucnak  končila vygenerováním SVG stop.

# Kroky:

- [x] Namodelování prototypu v OpenSCADU - @Alsa-Tucnak
- [x] Otestování vytištěných disků (sestavení) - @Alsa-Tucnak
- [ ] Export dat pro import do kicadu - Frézování  - @Alsa-Tucnak
- [ ] Export dat pro import do kicadu - Měděná vrstva  - @Alsa-Tucnak
- [ ] Export dat pro import do kicadu - Vrtané otvory - @Alsa-Tucnak
- [ ] Import všech dílčích dat do Kicadu - @ChroustJan
- [ ] Dokončení PCB (schéma, layout) - @ChroustJan

**Při všech importech do kicadu je potřeba importovat na určité souřadnice (screenshoty toto pravidlo nereflektují)**

## Postup

### Namodelování v OpenSCADu

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

Vytvoření řezu
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

Uložit jako svg:
Soubor -> Exportovat -> Exportovat jako SVG

Postup je potřeba opakovat pro všechny vrstvy. Tj. Obrys, měď, atd..

### Import do KiCADu

Otevřít Kicad - PCBnew
Vybrat ořezovou vrstvu
Soubor -> Import -> Grafika

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

Zde je potřeba vybrat správný soubor, Vybrat vrstvu pro frézavání (edge.Cuts), měřítka 1,0. Ideální je umístit SVG na určité souřadnice výkresu. Protože na stejné souřadnice se budou vkládat další modely.

Následně disk umístit do prostoru

V 3D náhledu bychom měli vidět toto:
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

Pokud bude potřeba definovat i plochu výplně, tak to se musí vytvořit vlastní openscad modul obsahujíci plochu měděné výplně˙
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

A tento objekt se chová jako měděná výplň. To se může hodit na přesné namodelování prostorů elektrod.

Otvory pro vrtání
Nevím o přímé cestě, jak vložit do kicadu otvorp pro vrtání. Je tedy nutné si pomoct tak, že v OpenSCADu se vygeneruji pomocné značky pro místa vrtání. To se naimportuje do kicadu, do nějaké uživatelské vrstvy. A v Kicadu se na tato místa vloží vrtané díry.

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

V kicadu následně umístit díry jako footprint:
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

kaklik, 2021-07-23:
[Zde jsem našel pána na youtube](https://youtu.be/hHURDpH471o?t=194), který má trik na to, jak díry v DXF zarovnat s footprinty děr tak, aby se ten střed nemusel hledat ručně.

kaklik, 2021-08-12:
Issue přesunuto sem: https://github.com/UniversalScientificTechnologies/THUNDERMILL01/issues/5 Aby jej bylo možné zařadit do projektu.

Closed 2021-08-12.

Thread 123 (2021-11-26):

Rotor failure - Drumroll emergency mode

kaklik, 2021-11-26:
The autogyro main emergency mode is continuous autorotation flight using the main rotor. The problem emerges in the case of main rotor failure (seizure of bearing, shaft/pylon cracks, etc. ).

TF-G2 construction with the absence of a horizontal stabilizer is capable to do ["drumroll landing"](https://www.youtube.com/watch?v=i669PHLPcq8). It is rotation mode that effectively slows the descent rate by converting a significant portion of potential energy to aerodynamically damped rotation.
The net result is significantly decreased impact speed compared to crashes where spinning is not present.

Unfortunately, this mode needs to be enabled by immediate deactivation of the main engine. This should be done by autopilot, because the human pilot is not capable of that without notice of previous signs of rotor failure.

Therefore the FC should deactivate the main engine if multiple signs of rotor failure are present.

- Rotor RPM is zero
- Rotor vibrations are not present
- Level flight cannot be achieved (Acceleration is close to zero - free fall)

roman-dvorak, 2021-11-26:
Super.. myslím, že bychom měli začít vytvořením nějakého drumroll detektoru.

kaklik, 2021-11-26:
> Super.. myslím, že bychom měli začít vytvořením nějakého drumroll detektoru.

Já doufal, že tohle bude řešit někdo úplně jinej. Proto jsem to psal anglicky. :D

kaklik, 2023-08-16:
Kromě přistání, tak i pro tento účel by se hodilo, kdyby vírník měl za letu odpojitelný rotor.  Jeho odpojením by bylo možné vyřešit následující situace:

- Okamžité ukončení letu v kritické situaci (např. bezpečnostní situace, kdy hrozí kolize, nebo vstup do zakázaného prostoru)
   - Jde tím otestovat a následně použít relativně bezpečný mód pádu v ploché vývrtce, jak je popsáno výše
- Zjednodušení algoritmu přistání. Neboť odhozením rotoru těsně nad zemí se vyřeší problém "co s energií v rotoru po dosednutí".

Technicky jsou dva možné způsoby realizace. První je použití serva pro odjištění ložiskového sloupku rotoru. Druhá možnost je tepelné oddělení plastové pojistky, která bude držet sloupek rotoru.

V případě použití serva, je softwarová realizace celkem přímočará, protože lze použít přímo některý volný PWM výstup. V případě tepelného aktuátoru řešení už tak jednoznačné není, protože PX4 na to nemá přímo vyřešený ovladatelný výstup. Bylo by nutné použít nějaké náhradní řešení například přes  [camera trigger](https://docs.px4.io/main/en/peripherals/camera.html#trigger-interface-backends). [Padáková logika implementovaná v PX4](https://docs.px4.io/main/en/peripherals/parachute.html) zdá se problém nijak neřeší, prototože předpokládá použití PWM výstupu v režimu serva.

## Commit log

2019-10-13 Auto stash before merge of "master" and "origin/master"
    [888_1001.scad, 888_1005.scad, parameters.scad]
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2020-02-17 Fix undeffined mirror image.
    [888_1003.scad]
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2020-04-10 Import dilu rotorove, hlavy, uprava ramecku, uprava dilu rot. hlavy
    [888_1008.scad, 888_1009.scad, 888_1010.scad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]
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2020-04-25 Uprava sestav podlozky a bocni steny, zmena odlehceni
    [888_1001.scad, 888_1003.scad, assembly.scad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]
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2020-05-12 fix typo
    [888_1003.scad, 888_1007.scad, 888_1008.scad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]
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2020-05-22 shorter bearing holder #17
    [888_1013.scad]
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2020-05-25 oprava odečtu - válec nahrazen jehlanem doplnění koncovek
    [888_2002.scad]
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2020-06-26 Uprava bocnice - odebrani stredni pricky pro lepsi montaz krytu.
    [888_1007.scad, printplate_888_1007.amf, printplate_888_1007.stl]
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2020-07-16 Resolve #57 Rozšířena a zaoblena trhací placka rotoru.
    [888_1014.stl, 888_3001.stl, 888_3002.stl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]
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2020-07-16 fixed: #51
    Tloušťka tiskové vrstvy snížena a vytvořena speciální konfigurace pro tisk úhlových podložek.
    [printplate_888_4006_-1_5.amf, printplate_888_4006_-1_5.scad, printplate_888_4006_-1_5.stl]
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2020-07-17 Add new rpm sensor cap, with rope prerotator cylinder, combined with bottom part of central part of rotor.
    [888_4008.scad, compare_cap.scad]
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2020-07-17 Fix bug in prinplate positioning.
    [printplate_888_4003.amf, printplate_888_4003.scad, printplate_888_4003.stl]
2020-07-17 Slicing fixed print-plate.
    [printplate_888_4003.amf]
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2020-07-23 Zvětšení tolerance pro výztuhy uvnitř listů.
    [parameters.scad, printplate_888_4001_a.amf, printplate_888_4001_a.stl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]
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2020-08-20 Parameters reordering and cleanup without changing parameters values.
    [parameters.scad]
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2020-08-20 Fix tolerancí i v dílu A.
    Zvětšení rozlišení povchu profilu.
    [888_4001.scad, printplate_888_4001_a.scad, printplate_888_4001_bcd.scad]
2020-08-21 Vylepšení tisknutelnosti listu issue #2
    [parameters.scad, printplate_888_4001_a.amf, printplate_888_4001_a.stl]
2020-08-21 Zlepšení parametrů tisku
    https://github.com/ThunderFly-aerospace/PrintedRotor/issues/2
    [parameters.scad, printplate_888_4001_a.amf, printplate_888_4001_bcd.amf]
2020-08-31 Prořezy - posunutí o určitý úhel Prolomení - nastavení úhlu "angle" na 55°
    [888_2002.scad]
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2020-09-03 Snížení tolerance pro výztuhy listů.
    [parameters.scad]
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2020-10-06 Resolve #66
    [888_4007.scad, printplate_888_4007.amf, printplate_888_4007.stl]
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2020-10-28 Uprava airspeed, priprava na vicko, ramecek okolo pcb
    [888_5001.scad, printplate_888_5001.amf, printplate_888_5001.scad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]
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2020-11-25 Fix #75
    [888_4002.scad, printplate_888_4002.amf, printplate_888_4002.stl]
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2020-11-25 pridani diry na zastrceni provazku do rolnicky #58
    [888_4008.scad, printplate_888_4008.amf, printplate_888_4008.stl]
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2020-12-01 888_1003 shape simplification
    (cherry picked from commit c1d69dac6168eeaf152ade785b3aff73aa42e194)
    [888_1003.scad, printplate_888_1003a.scad, printplate_888_1003a.stl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]
2020-12-01 888_1003 split position adjust
    (cherry picked from commit 90dbcc68123bf50522634f2b9415188e4a1910e0)
    [888_1003.scad, printplate_888_1003a.scad, printplate_888_1003a.stl]
2020-12-01 Fix #75
    (cherry picked from commit a59cde56f261afa749246cdc747a7ac4d992294c)
    [888_4002.scad, printplate_888_4002.amf, printplate_888_4002.stl]
2020-12-01 Usnadneni montaze rotoru #74
    (cherry picked from commit faa394a93dbd03f03c1f06ea2aab26dd876d74bc)
    [888_4006.scad, printplate_888_4006_-0_5.amf, printplate_888_4006_-0_5.stl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]
2020-12-01 Revert "888_1003 split position adjust"
    This reverts commit 90dbcc68123bf50522634f2b9415188e4a1910e0.
    [888_1003.scad, printplate_888_1003a.scad, printplate_888_1003a.stl]
2020-12-01 Revert "888_1003 shape simplification"
    This reverts commit c1d69dac6168eeaf152ade785b3aff73aa42e194.
    [888_1003.scad, printplate_888_1003a.scad, printplate_888_1003a.stl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]
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2020-12-03 ThunderFly-aerospace/TF-G2#16 Modifying PCB lid in 888_5001.scad to be aerodynamic. Work in progress.
    [888_5001.scad, bolt_parameters.scad]
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2020-12-03 Uprava spodni casti pylonu a priprava na tisk pro 6 mm trubicky
    [parameters.scad, printplate_888_1007-888_1008.amf, printplate_888_1007-888_1008.scad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]
2020-12-08 Prehozeni popisku rotorovych listu na vrchni stranu. #74
    [888_4001.scad]
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2021-01-11 ThunderFly-aerospace/TF-G2#9 Updated functions in front landing gear. Code clean-up. Work in progress.
    [888_2002.scad]
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2021-01-20 ThunderFly-aerospace/TF-G2#9 Fixed hole for wheel screw, resized triangles to keep more material on top/bottom of the leg, mirrored print bed cut to make the leg symmetrical.
    [888_2002.scad]
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2021-01-22 ThunderFly-aerospace/TF-G2#9 Rotated 888_2002 to flatten it on print plate and reduced length of landing gear block.
    [888_2002.scad]
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2021-02-02 Split landing gears holder in printplate. #9 Increase displacement of mounting screws.
    [888_2002.scad, printplate_888_2002.amf, printplate_888_2002.scad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]
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2021-02-09 Revert increased distance of mounting holes.
    [888_2002.scad, printplate_888_1002.amf, printplate_888_1002.stl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]
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2021-02-09 Add second pair of mounting holes.
    Improve screw holes position .
    [888_2002.scad]
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2021-02-09 Fix 3D printing out of the printing bed.
    [printplate_888_2002.amf, printplate_888_2002.scad, printplate_888_2002.stl]
2021-02-19 Imrove tightness against light. #64
    [888_4008.scad]
2021-02-19 Resolve hole in top of rope starter #64
    [888_4008.scad]
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2021-03-06 Decrease marging between sensonsor and rotating cylinder. #64
    [888_1012.scad]
2021-03-16 switch to stable openscad version. Add correct folder path to add png images.
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2021-03-29 Decrease of strengh of tail tube mount #92
    [888_3006.scad]
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2021-05-09 #97 - fixed - embedding of M3 nut in 1002
    [888_1002.scad]
2021-05-10 #97 - add screw head embedding to 1002
    [888_1002.scad, 888_1003.scad, parameters.scad]
2021-05-13 Add light blocking rim to the rotor mount.
    [888_1012.scad]
2021-05-14 Improve resolution of issue #103.
    [888_1012.scad, printplate_888_1012.scad]
2021-05-14 Improve tolerances for #102
    [888_1011.scad, 888_1012.scad, position_rotorhead.scad]
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2021-05-25 Add an experimantel free flap head - only for primary testing, not finished, not tested
    [888_4009.scad, 888_4010.scad]
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2021-05-29 Workflow improvement (#108)
    * Automatic commit from workflow
    * delete travis file
    * uprava struktury slozky s konfiguraci
    * gitignore
    * Automatic commit from workflow
    * Update printable_files.ym
    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
    [888_1002.stl, 888_1010.scad, 888_1010.stl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]
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2021-06-13 Add colective as text to free flap blade holder
    [888_4010.scad, parameters.scad]
2021-06-16 Removing special block on sides to mount landing gear it will be replaced by separate part.
    [888_1003.scad]
2021-06-16 Add a new part for landing gear mount. Part 888_2004 from branch mini.
    [888_2004.scad]
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2021-06-16 Adding prinplate to 888_2004 from mini branch. #109
    [printplate_888_2004.scad]
2021-06-16 Improve resolution of holes in the prinplate #86
    [888_2004.scad, printplate_888_2004.scad]
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2021-06-16 Translate comment in print plate
    Trigger the gcode generation.
    [printplate_888_1010.scad]
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2021-06-17 Fix printing configuration.
    [printplate_888_1009.scad, printplate_888_1018.scad, printplate_888_1101.scad]
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2021-06-18 Fix path to slicing profile.
    [printplate_888_1020.scad]
2021-06-18 solve some issues and warning
    [888_1010.scad, assembly_pylon.scad, assembly_rotor_head.scad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]
2021-06-18 Different pockets for nuts around rotor axis and holes for sefl-cutting screws for thundermill
    [888_4008.scad]
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2021-07-27 setup real ax and bearings, add M2 screws for ax fixing
    [888_4010.scad, parameters.scad]
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2021-08-01 Move the 3D printed rotor sources to a submodule to make it reusable across multiple autogyro versions.
    [888_4001.scad, 888_4102.scad]
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2021-08-13 Improve stiffness of tail tube holder. #101 #116
    [888_3006.scad, parameters.scad]
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2021-08-13 Remove unwanted material bellow the rudder. Resolve #116
    [888_3001.scad, 888_3004.scad]
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2021-08-16 Fix collision in printplate.
    [printplate_888_3006.scad]
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2021-08-17 Improve free flap after first weight tests - place for iron rod in blade, tune place for blade ax screws
    [888_4009.scad, 888_4010.scad, assembly_freeflap.scad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]
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2021-08-19 Copy improvements form 2 blades into 4 blades shaft. Fix ax length in 2 blade version
    [888_4009.scad, 888_4009_4_blades.scad]
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2021-08-31 shell mounting rim on the top of motor holder decrease amount of material used.
    [888_1002.scad]
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2021-09-06 Fix issue with limiting backwall in motor holder.
    [888_1002.scad, printplate_888_1002_-3.scad]
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2021-09-09 Decrease scratch depth by half. Fix #118
    [888_1009.scad]
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2021-09-16 Attempt to resolve #98
    [888_2002.scad]
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2021-09-19 Fix missing parameters for chassi sides. Include tail tube mounting assembly.
    [888_1003.scad, assembly_chassi.scad, position_888_1021.scad]
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2021-09-27 Fix clearance issues.
    [888_3001.scad, 888_3002.scad]
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2021-10-05 set same direction of all blade parts along y ax, for better quality on Mini
    [printplate_888_4001_bcd.scad]
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2021-10-25 Imroved battery holder - decreased weight - New hole for battery balancer connector
    [888_1018.scad, assembly_chassi.scad, position_888_1018.scad]
2021-10-26 Resolve issue #121
    [888_1018.scad]
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2021-10-26 fix syntax error.
    [888_4009.scad]
2021-11-02 Fix object manifold issue https://github.com/ThunderFly-aerospace/processor3D/issues/21
    [888_1018.scad]
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2022-01-13 fix intersection in wheels printplate.
    [printplate_888_2003.scad]
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2022-05-16 Fix rotor head parst position, and connector of pitch and roll ax. Need test..
    [888_1010.scad, 888_1011.scad, assembly.scad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]
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2022-05-16 fix 888_1012 bug from code simplification, need tests.. improve position of parts
    [888_1012.scad, position_888_1012.scad]
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2022-05-27 Fix Rotor head neck height
    [parameters.scad]
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2022-07-26 move tail pipe 1mm down, to increase probabilit of breaking part 3006
    [888_3006.scad]
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2022-10-25 Tune base to avoid damage by tail tube.
    [888_1001.scad]
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2022-12-29 replace screew with nut
    [888_4009.scad]
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2023-01-04 try to fix printing probelms with free-flap
    [888_4009.scad, 888_4010.scad, parameters.scad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]
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2023-01-04 Try to fix freeflap (print issue on 4010 and bad upgrade on 4009)
    [888_4009.scad, 888_4010.scad]
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2023-08-11 #28 - fix paths and resolution for generated pngs from blender
    [assembly.scad, assembly_888_test.scad, assembly_chassi.scad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]
2023-08-11 Revert "Automatic commit from workflow"
    This reverts commit 3982b2615c0712da52b43f9f101035d5b2093e38.
    [888_1002.stl, 888_1010.stl, 888_1018.stl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]
2023-08-11 #28 fix place of blender's images and other files
    [TF-G2_assembly_assembly_888_test.blend, assembly_888_test.stl, assembly_freeflap.stl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]
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2023-08-28 Remove rotor nut clearances.
    [888_4008.scad]
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2023-08-28 Update printable_files.yml
    Revert update of Ubuntu version to 20.04
